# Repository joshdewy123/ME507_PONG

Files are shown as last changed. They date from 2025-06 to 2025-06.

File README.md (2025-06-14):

# ME 507 - Ping Pong Ball Launcher

**Team Members:** Josh DeWeese, Nolan Jeung  
**Support:** Charlie Refvem, Vincent Ngo, Jason Wong

---

**Link to repository:** https://github.com/joshdewy123/ME507_PONG

**Link to video:** https://youtube.com/shorts/3GikZNkVesM?feature=share

---

## Overview

This autonomous ping pong launcher is capable of both manual and automatic targeting and launching. It rotates about two axes to aim, detects objects using a TF-Luna LIDAR, and fires ping pong balls using dual flywheels. The system is built around a custom PCB featuring an STM32 microcontroller, motor drivers, and dedicated I2C lines.

The goal of this project was to create a functional and robust autonomous targeting system while designing and assembling most of the electronics and mechanical components from scratch.

---

## Hardware (Mechanical)

The robot was designed to use primarily hardware already in our possession in order to be cost-efficient, since the robot was not anticipated to pull extremely heavy loads anyways. The list of actuators and their purposes are below:

- **2x Pololu 50:1 Gearmotor (4753):** – 12V DC motor with built-in encoders to control the turret/aiming of the robot. Their reasonable size and torque made them a viable choice for this project.
- **2x Maxon DCX 22 mm OD Motors:** - 18V DC motor with no external gearbox or sensors. They are able to reach up to about 5000 RPM at nominal speeds, making them a great choice for our flywheels. Despite their nominal voltage of 18V, they were run using 12V instead to limit the necessary power redistribution of our electronics.
- **1x MG90 Servo Motor:** - simple 5V servo motor used to control ball loading and launching. Moves to certain angles dependent on the signal sent to it. They were used to push balls forward into the launcher while blocking the next ball from launching at the same time, providing the robot functionality to control when and the quantity of balls launched.

The rest of the robot was constructed using a combination of 3-D printed and off-the-shelf components. The robot implements a modular design to allow for easy re-design, removal, and reattachment of components when necessary. Power transfer between the launcher and motors was achieved using belts, pulleys, hand-cut shafts, and bearings. All fasteners are a combination of M2, M2.5, or M3 screws when necessary, and heat-set inserts were used in many locations for ease of assembly and a high overall quality of work.

Small attachment parts were made during the project’s development, and they proved to be very important. First, the flywheels were simply 3-D printed to attach to the Maxon DCX motor’s shaft, as well as be supported by bearings below. Launcher compression was achieved using super-glued foam strips around the wheels. Secondly, the different tensioners were created to improve the grip of the belt-pulley systems. On initial testing, the motors did not have enough tension with the components they were meant to move. Tensioners were added and vastly improved the power transfer of the robot.

Overall, the mechanical design of the robot worked very well. The magazine, launcher, and ball loading mechanism worked especially well. Power transfer between the motors and other components worked well, but over time, the plastic 3-D printed components began losing their grip on the metal shafts, causing more slip over time. If the project were continued with moree time and budget, the robot would utilize more metal mechanical components for longevity.

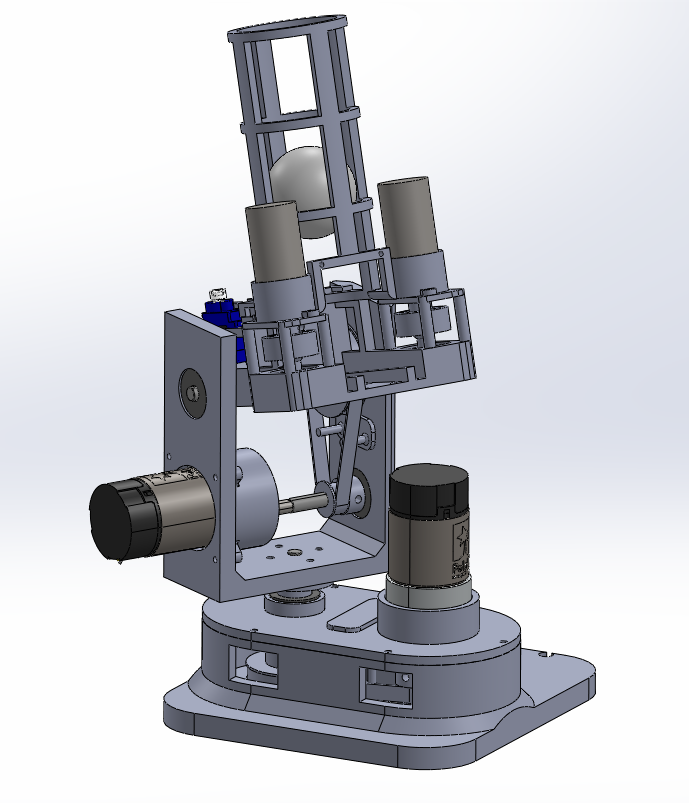
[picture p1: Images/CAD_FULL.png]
Full Mechanical System Model


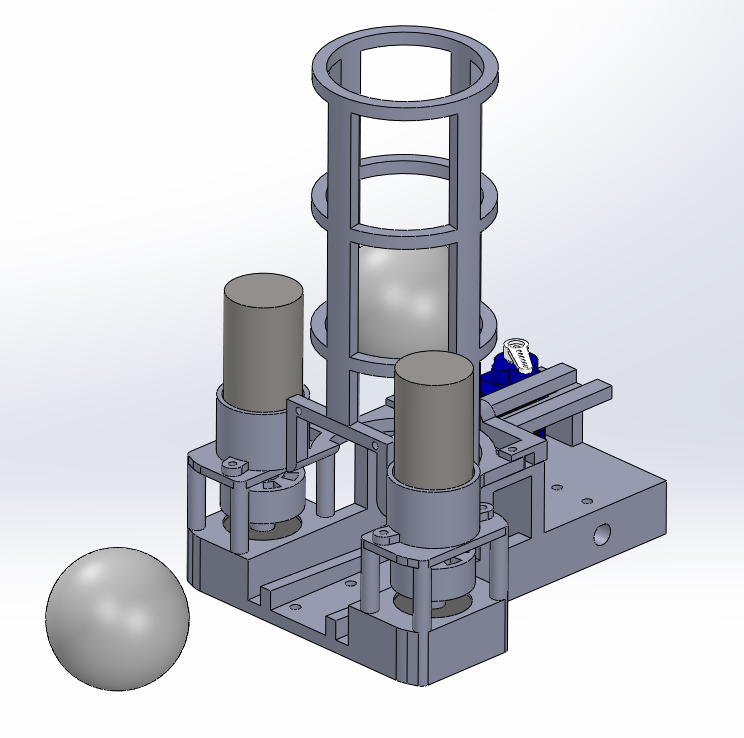
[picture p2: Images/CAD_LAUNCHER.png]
Launcher Portion of the Mechanical System Model


---

## Hardware (Electrical)

### Fusion 360 Schematics

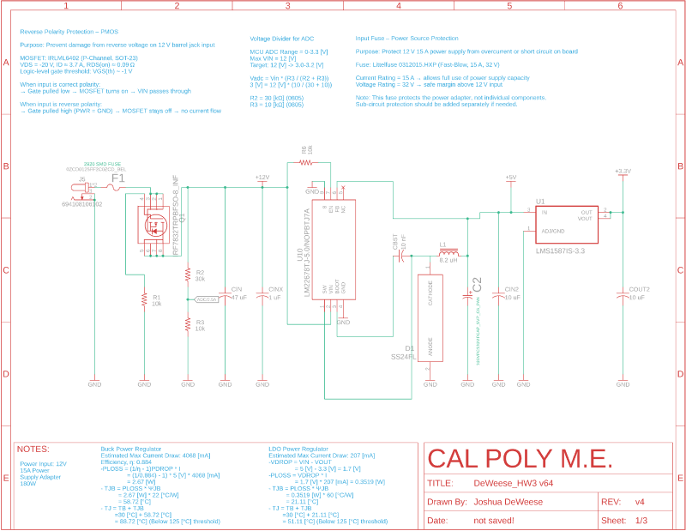
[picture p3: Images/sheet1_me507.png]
Power Regulation


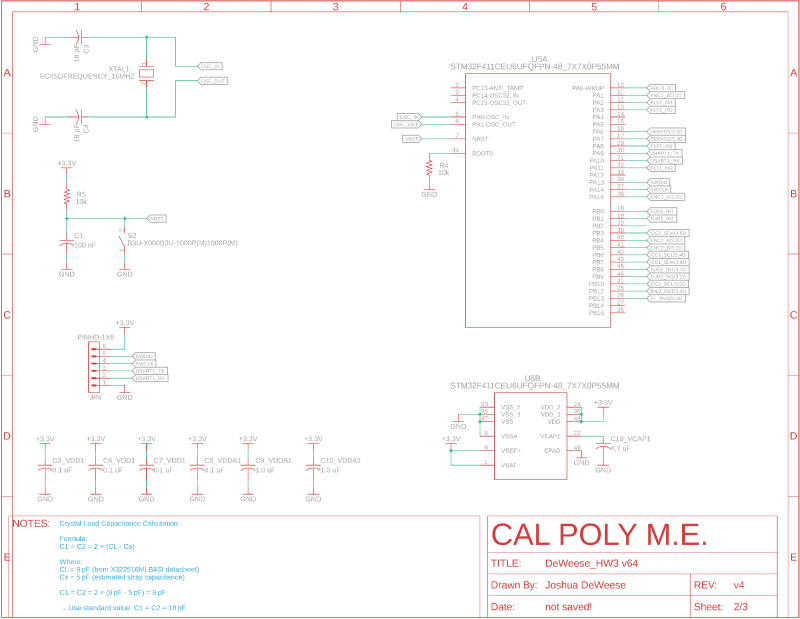
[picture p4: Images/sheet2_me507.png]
MCU Pinouts


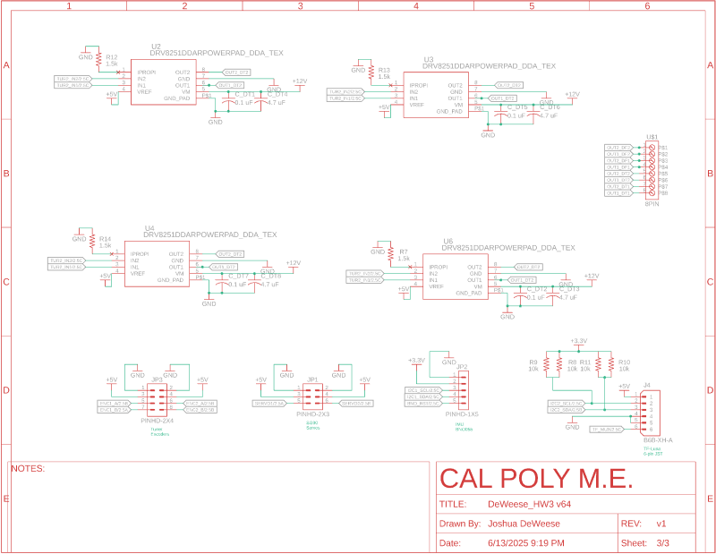
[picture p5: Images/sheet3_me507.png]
Motor Drivers w/ Sensor + Actuator Outputs


### Fusion 360 CAD Render

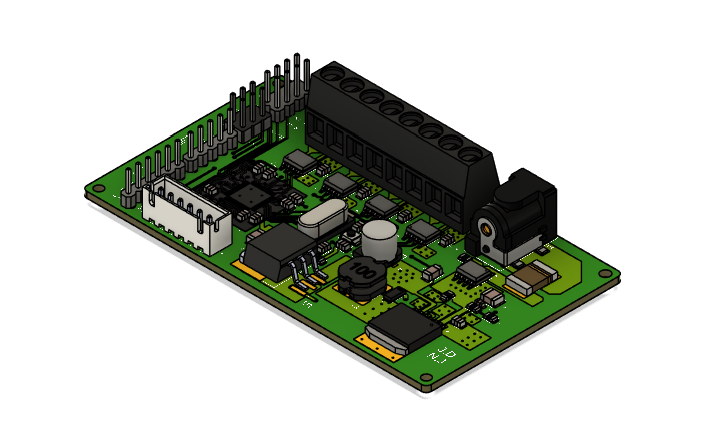
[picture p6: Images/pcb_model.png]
PCB CAD Model


### Assembled PCB - Before Hotfixes

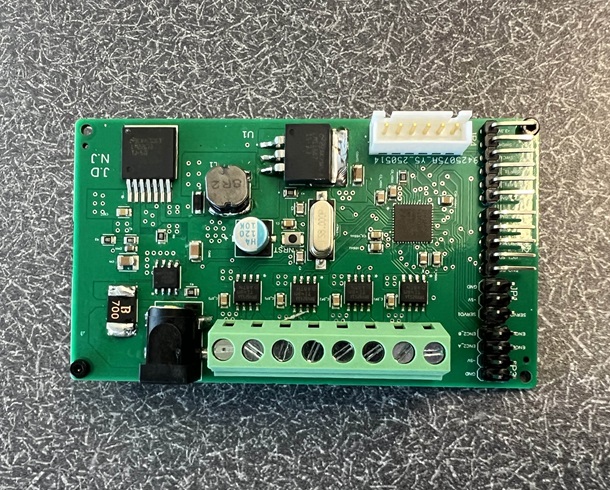
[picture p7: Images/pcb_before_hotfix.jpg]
Before Fix


### Assembled PCB - After Hotfixes

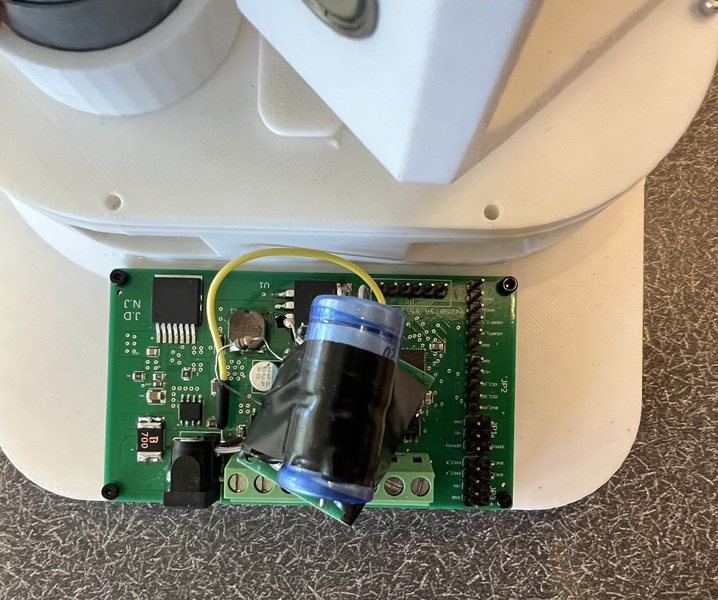
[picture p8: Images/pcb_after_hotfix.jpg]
After Fix


**This board includes:**

- STM32F411CEU6 microcontroller
- DRV8251 motor drivers
- Barrel jack for 12V input
- 5V and 3.3V rails (via Buck and LDO regulators)
- I2C, UART, and GPIO breakout headers

---

## Roadblocks and Debugging Challenges

### 1. **Motor Driver Output Failures**

**Issue:** Turret motor driver (DRV8251) failed to drive motors consistently.

**Cause:** Missing or insufficient bulk capacitance and improper IPROPI pin handling.  
**Fix:**

- Added 0.1 µF and 4.7 µF capacitors to stabilize power rails
- Pulled IPROPI to GND through a 1.5kΩ resistor

#### Fusion Schematic Before Fix

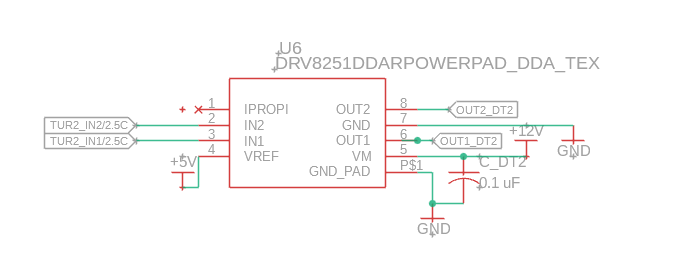
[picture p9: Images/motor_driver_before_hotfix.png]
Motor Driver Schematic Before


#### Fusion Schematic After Fix

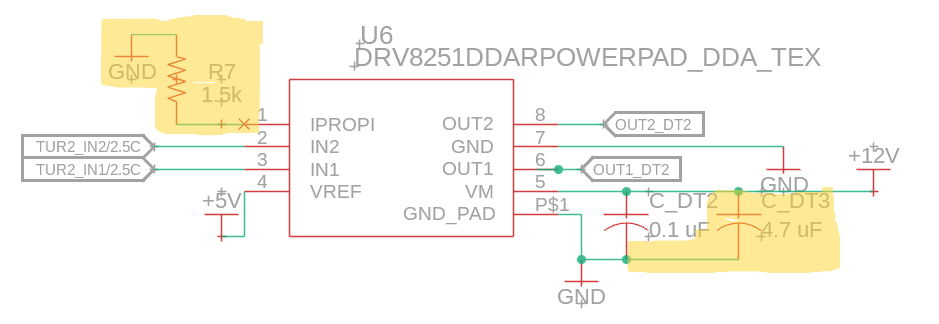
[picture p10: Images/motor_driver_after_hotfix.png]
Motor Driver Schematic After


---

### 2. **LIDAR Inconsistent I2C Behavior**

**Issue:** TF-Luna LIDAR would intermittently drop off the I2C bus.  
**Cause:** No pull-up resistors on SDA and SCL lines.  
**Fix:** Manually added 10kΩ pull-ups from both lines to 3.3V.

#### Fusion Schematic Before Fix

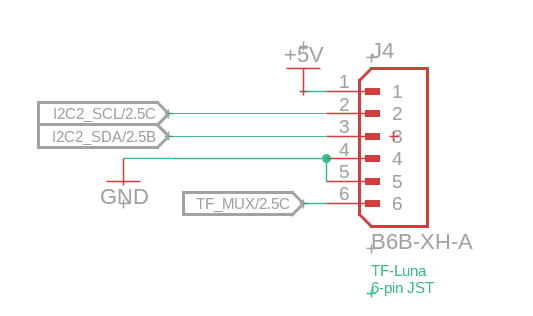
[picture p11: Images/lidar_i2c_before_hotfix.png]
LIDAR Schematic Before


#### Fusion Schematic After Fix

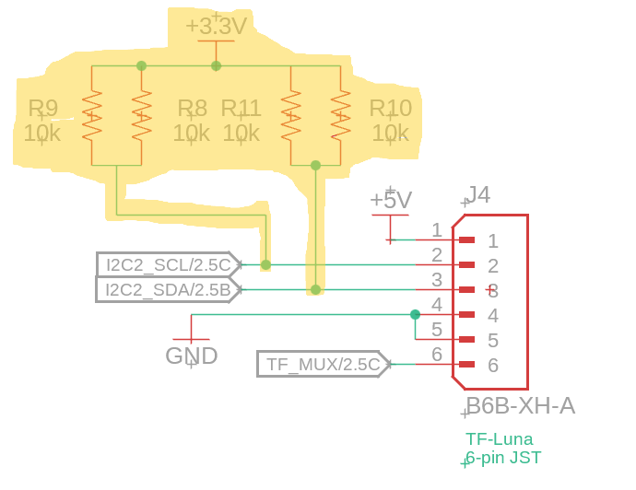
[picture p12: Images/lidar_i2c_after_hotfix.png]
LIDAR Schematic After


#### Physical Pull-up Resistor Fix (3 Angles)

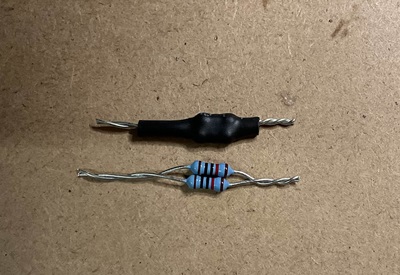
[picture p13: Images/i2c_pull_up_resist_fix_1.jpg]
Pull-up Fix 1
  
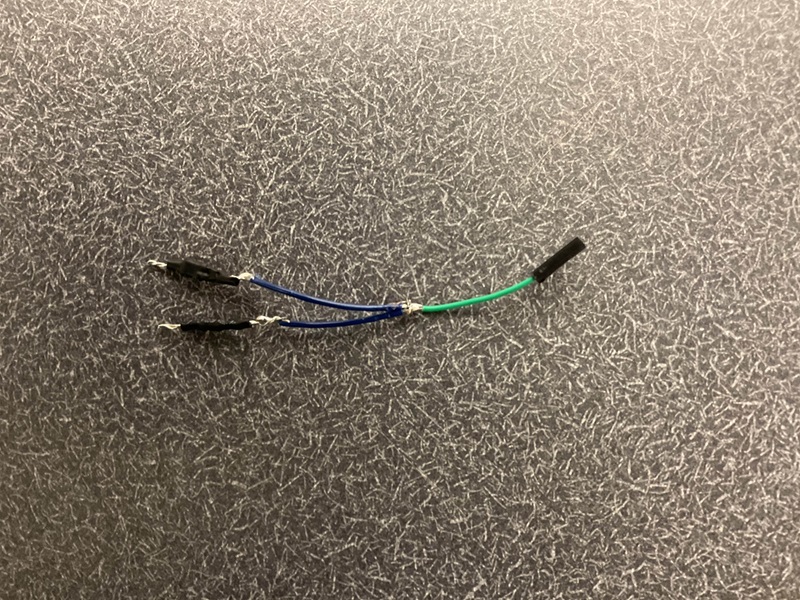
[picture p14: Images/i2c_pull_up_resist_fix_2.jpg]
Pull-up Fix 2
  
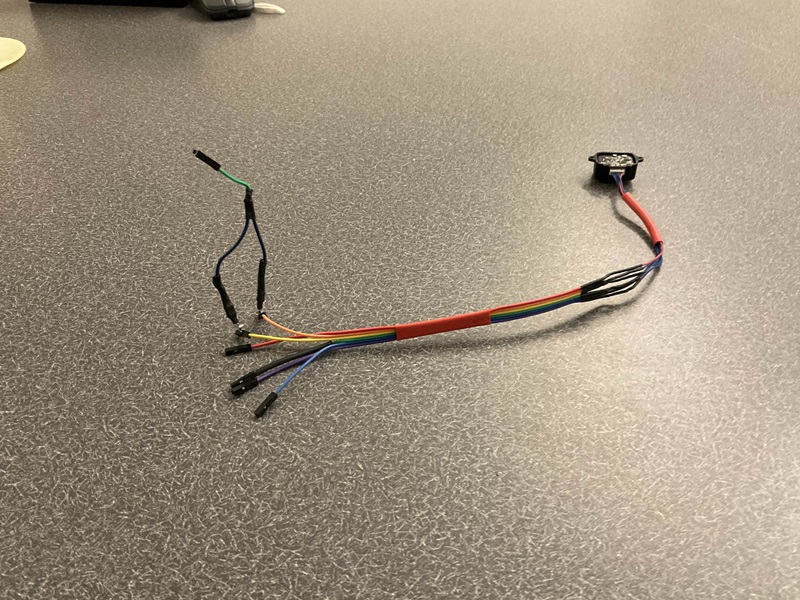
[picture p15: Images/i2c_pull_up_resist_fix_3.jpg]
Pull-up Fix 3


---

## Software Implementation

The robot was programmed in C only, as updating the project to C++ caused various issues to occur. The program features a few drivers, a primary main loop, and a finite state machine inside of the main loop. Some primary features of the program include:

- **Software PWM:** - created due to lack of timers on hardware pins for the servo motor. It functions by setting the pin to high or low depending on the system’s core clock using switch states. While this is not as accurate as hardware PWM, it was OK to use for the servo motor, since its usage was not a primary development focus and it just needed to move back and forth. However, it did cause the program to not support any HAL delays in the main loop or functions due to it causing the servo to move. This function would be removed in future iterations of the robot if possible.
- **Main Loop:** - used to run both the finite-state-machine and a few functions that always need to be called for accuracy. The main loop always updates both turret encoders and converts the ticks into degrees. It also updates the servo software pwm. If the BNO055 is implemented, it would also update the euler angles in this portion as well.
- **Finite State Machine:** - The FSM has 6 states, also described in the diagram. Entering the commands (COMM) into the console triggers different states.
- Initialization, moves the turret motors to a more optimal angle for later movements. See the link: https://youtube.com/shorts/3GikZNkVesM?feature=share
- State 1: Hub, waiting for commands to be entered in the PUTTY console
- State 2: Aim, moves the turret motors to desired angle
- State 3: Lidar, reads the current distance and amp values from the laser sensor
- State 4: Fly, spins the flywheel motors to a set duty
- State 5: Launch, launches the ball currently loaded in a sequence of movements
- State 6: Auto scan, an autonomous routine to scan the area using a set of movements and lidar scan stored data. Scans area, moves to closest distance, launches the ball, then returns to State 1.

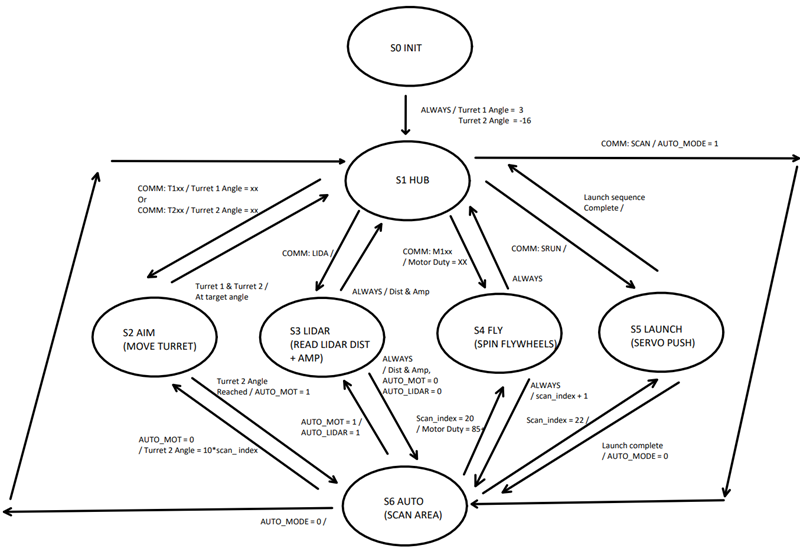
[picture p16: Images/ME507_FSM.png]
FSM Diagram


- **Commands:**
- M1xx (or M2xx) (S4): sets the duty cycle of the flywheels to the percent hex xx value.
- T1xx / T2 xx (S2): sets the desired value for the respective turret to the hex xx value.
- LIDA (S3): returns the lidar sensor values: distance (in cm) and amp (determines validity of reading).
- SRUN (S5): servo routine to launch the ball.
- SCAN (S6): autonomous scan routine

---

## Future Work

If this project were continued, there are multiple fixes to be implemented that would greatly improve the consistency and functionality of the robot:

- **Improve material choices and design:** - Physical slop between the shafts and 3-D printed components developed over time when operating the robot. By adding more metal components or inserts to connect the shafts to 3-D printed components, the removed slop would improve the encoder angle reading accuracy and ensure proper movement when intended.
- **Review datasheets to optimize PCB design:** - Because of the hotfixes implemented to make the motor drivers functional on the PCB, there were more temperature and motor driver overcurrent than intended. This sometimes caused the motors to not run when intended when the robot was left on for extended periods of time. This would also sometimes cause the robot to get stuck in certain states due to not reaching its intended motor angles. If the current sensing resistors and bulk capacitors were more properly implemented into the PCB design, the motor driver would be much more consistent, leading to easier testing and functionality over time.
- **Implement BNO055 (IMU) logic:** - Since the IMU is attached to the end of the launching mechanism, its angle readings would be more accurate than the encoder readings. It would also account for the physical slop, which the motors could then compensate for in a control loop. However, even though the IMU was functional, there was not time to implement refined control loops using the IMU readings.
- **Improve UI:** - The PUTTY console UI was usable and had all the necessary functionality. However, an actual UI using buttons instead of commands would be more intuitive. Additionally, wireless control would be beneficial for ease of use.

---

## Repository Structure

```
ME507_PONG
├── CAD_MECHANICAL_SYSTEM/      # CAD files for mechanical design
├── Core/                       # Main firmware source code (.c/.h)
├── Drivers/                    # Device drivers (e.g. HAL, custom)
├── Images/                     # Images for Doxygen/README
├── docs/                       # GitHub Pages deployment folder
│   └── index.html              # Doxygen homepage
├── .gitignore                  # Excludes build & local files
├── .project, .cproject         # Eclipse project configs
├── .mxproject                  # STM32CubeMX project file
├── README.md                   # Project overview and documentation
├── STM32F411CEUX_FLASH.ld      # Linker script (FLASH region)
├── STM32F411CEUX_RAM.ld        # Linker script (RAM region)
└── Term_Project_3.ioc          # STM32CubeMX configuration file
```

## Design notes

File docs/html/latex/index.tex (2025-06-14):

\chapter{ME 507 -\/ Ping Pong Ball Launcher }
\hypertarget{index}{}\label{index}\index{ME 507 -\/ Ping Pong Ball Launcher@{ME 507 -\/ Ping Pong Ball Launcher}}
\label{index_md__r_e_a_d_m_e}%
\Hypertarget{index_md__r_e_a_d_m_e}%

{\bfseries{Team Members\+:}} Josh De\+Weese, Nolan Jeung ~\newline
 {\bfseries{Support\+:}} Charlie Refvem, Vincent Ngo, Jason Wong

\DoxyHorRuler{0}

{\bfseries{Link to repository\+:}} \href{https://github.com/joshdewy123/ME507_PONG}{\texttt{https\+://github.\+com/joshdewy123/\+ME507\+\_\+\+PONG}}

{\bfseries{Link to video\+:}} \href{https://youtube.com/shorts/3GikZNkVesM?feature=share}{\texttt{https\+://youtube.\+com/shorts/3\+Gik\+ZNk\+Ves\+M?feature=share}}

\DoxyHorRuler{0}
\hypertarget{index_autotoc_md3}{}\doxysection{\texorpdfstring{Overview}{Overview}}\label{index_autotoc_md3}
This autonomous ping pong launcher is capable of both manual and automatic targeting and launching. It rotates about two axes to aim, detects objects using a TF-\/\+Luna LIDAR, and fires ping pong balls using dual flywheels. The system is built around a custom PCB featuring an STM32 microcontroller, motor drivers, and dedicated I2C lines.

The goal of this project was to create a functional and robust autonomous targeting system while designing and assembling most of the electronics and mechanical components from scratch.

\DoxyHorRuler{0}
\hypertarget{index_autotoc_md5}{}\doxysection{\texorpdfstring{Hardware (Mechanical)}{Hardware (Mechanical)}}\label{index_autotoc_md5}
The robot was designed to use primarily hardware already in our possession in order to be cost-\/efficient, since the robot was not anticipated to pull extremely heavy loads anyways. The list of actuators and their purposes are below\+:

\begin{DoxyItemize}
\item {\bfseries{2x Pololu 50\+:1 Gearmotor (4753)\+:}} – 12V DC motor with built-\/in encoders to control the turret/aiming of the robot. Their reasonable size and torque made them a viable choice for this project.
\item {\bfseries{2x Maxon DCX 22 mm OD Motors\+:}} -\/ 18V DC motor with no external gearbox or sensors. They are able to reach up to about 5000 RPM at nominal speeds, making them a great choice for our flywheels. Despite their nominal voltage of 18V, they were run using 12V instead to limit the necessary power redistribution of our electronics.
\item {\bfseries{1x MG90 Servo Motor\+:}} -\/ simple 5V servo motor used to control ball loading and launching. Moves to certain angles dependent on the signal sent to it. They were used to push balls forward into the launcher while blocking the next ball from launching at the same time, providing the robot functionality to control when and the quantity of balls launched.
\end{DoxyItemize}

The rest of the robot was constructed using a combination of 3-\/D printed and off-\/the-\/shelf components. The robot implements a modular design to allow for easy re-\/design, removal, and reattachment of components when necessary. Power transfer between the launcher and motors was achieved using belts, pulleys, hand-\/cut shafts, and bearings. All fasteners are a combination of M2, M2.\+5, or M3 screws when necessary, and heat-\/set inserts were used in many locations for ease of assembly and a high overall quality of work.

Small attachment parts were made during the project’s development, and they proved to be very important. First, the flywheels were simply 3-\/D printed to attach to the Maxon DCX motor’s shaft, as well as be supported by bearings below. Launcher compression was achieved using super-\/glued foam strips around the wheels. Secondly, the different tensioners were created to improve the grip of the belt-\/pulley systems. On initial testing, the motors did not have enough tension with the components they were meant to move. Tensioners were added and vastly improved the power transfer of the robot.

Overall, the mechanical design of the robot worked very well. The magazine, launcher, and ball loading mechanism worked especially well. Power transfer between the motors and other components worked well, but over time, the plastic 3-\/D printed components began losing their grip on the metal shafts, causing more slip over time. If the project were continued with moree time and budget, the robot would utilize more metal mechanical components for longevity.

\begin{DoxyImage}

\doxyfigcaption{Full Mechanical System Model}
\end{DoxyImage}

\begin{DoxyImage}

\doxyfigcaption{Launcher Portion of the Mechanical System Model}
\end{DoxyImage}

\DoxyHorRuler{0}
\hypertarget{index_autotoc_md7}{}\doxysection{\texorpdfstring{Hardware (Electrical)}{Hardware (Electrical)}}\label{index_autotoc_md7}
\hypertarget{index_autotoc_md8}{}\doxysubsection{\texorpdfstring{Fusion 360 Schematics}{Fusion 360 Schematics}}\label{index_autotoc_md8}
 
\begin{DoxyImage}

\doxyfigcaption{Power Regulation}
\end{DoxyImage}

\begin{DoxyImage}

\doxyfigcaption{MCU Pinouts}
\end{DoxyImage}

\begin{DoxyImage}

\doxyfigcaption{Motor Drivers w/ Sensor + Actuator Outputs}
\end{DoxyImage}
   \hypertarget{index_autotoc_md9}{}\doxysubsection{\texorpdfstring{Fusion 360 CAD Render}{Fusion 360 CAD Render}}\label{index_autotoc_md9}
 
\begin{DoxyImage}

\doxyfigcaption{PCB CAD Model}
\end{DoxyImage}
   \hypertarget{index_autotoc_md10}{}\doxysubsection{\texorpdfstring{Assembled PCB -\/ Before Hotfixes}{Assembled PCB -\/ Before Hotfixes}}\label{index_autotoc_md10}
 
\begin{DoxyImage}

\doxyfigcaption{Before Fix}
\end{DoxyImage}
   \hypertarget{index_autotoc_md11}{}\doxysubsection{\texorpdfstring{Assembled PCB -\/ After Hotfixes}{Assembled PCB -\/ After Hotfixes}}\label{index_autotoc_md11}
 
\begin{DoxyImage}

\doxyfigcaption{After Fix}
\end{DoxyImage}

{\bfseries{This board includes\+:}}

\begin{DoxyItemize}
\item STM32\+F411\+CEU6 microcontroller
\item DRV8251 motor drivers
\item Barrel jack for 12V input
\item 5V and 3.\+3V rails (via Buck and LDO regulators)
\item I2C, UART, and GPIO breakout headers
\end{DoxyItemize}

\DoxyHorRuler{0}
\hypertarget{index_autotoc_md13}{}\doxysection{\texorpdfstring{Roadblocks and Debugging Challenges}{Roadblocks and Debugging Challenges}}\label{index_autotoc_md13}
\hypertarget{index_autotoc_md14}{}\doxysubsection{\texorpdfstring{1. {\bfseries{Motor Driver Output Failures}}}{1. {\bfseries{Motor Driver Output Failures}}}}\label{index_autotoc_md14}
{\bfseries{Issue\+:}} Turret motor driver (DRV8251) failed to drive motors consistently.

{\bfseries{Cause\+:}} Missing or insufficient bulk capacitance and improper IPROPI pin handling. ~\newline
 {\bfseries{Fix\+:}}

\begin{DoxyItemize}
\item Added 0.\+1 µF and 4.\+7 µF capacitors to stabilize power rails
\item Pulled IPROPI to GND through a 1.\+5kΩ resistor
\end{DoxyItemize}\hypertarget{index_autotoc_md15}{}\doxysubsubsection{\texorpdfstring{Fusion Schematic Before Fix}{Fusion Schematic Before Fix}}\label{index_autotoc_md15}
 
\begin{DoxyImage}

\doxyfigcaption{Motor Driver Schematic Before}
\end{DoxyImage}
   \hypertarget{index_autotoc_md16}{}\doxysubsubsection{\texorpdfstring{Fusion Schematic After Fix}{Fusion Schematic After Fix}}\label{index_autotoc_md16}
 
\begin{DoxyImage}

\doxyfigcaption{Motor Driver Schematic After}
\end{DoxyImage}

\DoxyHorRuler{0}
\hypertarget{index_autotoc_md18}{}\doxysubsection{\texorpdfstring{2. {\bfseries{LIDAR Inconsistent I2C Behavior}}}{2. {\bfseries{LIDAR Inconsistent I2C Behavior}}}}\label{index_autotoc_md18}
{\bfseries{Issue\+:}} TF-\/\+Luna LIDAR would intermittently drop off the I2C bus. ~\newline
 {\bfseries{Cause\+:}} No pull-\/up resistors on SDA and SCL lines. ~\newline
 {\bfseries{Fix\+:}} Manually added 10kΩ pull-\/ups from both lines to 3.\+3V.\hypertarget{index_autotoc_md19}{}\doxysubsubsection{\texorpdfstring{Fusion Schematic Before Fix}{Fusion Schematic Before Fix}}\label{index_autotoc_md19}
 
\begin{DoxyImage}

\doxyfigcaption{LIDAR Schematic Before}
\end{DoxyImage}
   \hypertarget{index_autotoc_md20}{}\doxysubsubsection{\texorpdfstring{Fusion Schematic After Fix}{Fusion Schematic After Fix}}\label{index_autotoc_md20}
 
\begin{DoxyImage}

\doxyfigcaption{LIDAR Schematic After}
\end{DoxyImage}
   \hypertarget{index_autotoc_md21}{}\doxysubsubsection{\texorpdfstring{Physical Pull-\/up Resistor Fix (3 Angles)}{Physical Pull-\/up Resistor Fix (3 Angles)}}\label{index_autotoc_md21}
 
\begin{DoxyInlineImage}
%Pull-\/up Fix 1
\end{DoxyInlineImage}

~\newline
  
\begin{DoxyInlineImage}
%Pull-\/up Fix 2
\end{DoxyInlineImage}

~\newline
  
\begin{DoxyInlineImage}
%Pull-\/up Fix 3
\end{DoxyInlineImage}

\DoxyHorRuler{0}
\hypertarget{index_autotoc_md23}{}\doxysection{\texorpdfstring{Software Implementation}{Software Implementation}}\label{index_autotoc_md23}
The robot was programmed in C only, as updating the project to C++ caused various issues to occur. The program features a few drivers, a primary main loop, and a finite state machine inside of the main loop. Some primary features of the program include\+:

\begin{DoxyItemize}
\item {\bfseries{Software PWM\+:}} -\/ created due to lack of timers on hardware pins for the servo motor. It functions by setting the pin to high or low depending on the system’s core clock using switch states. While this is not as accurate as hardware PWM, it was OK to use for the servo motor, since its usage was not a primary development focus and it just needed to move back and forth. However, it did cause the program to not support any HAL delays in the main loop or functions due to it causing the servo to move. This function would be removed in future iterations of the robot if possible.
\item {\bfseries{Main Loop\+:}} -\/ used to run both the finite-\/state-\/machine and a few functions that always need to be called for accuracy. The main loop always updates both turret encoders and converts the ticks into degrees. It also updates the servo software pwm. If the BNO055 is implemented, it would also update the euler angles in this portion as well.
\item {\bfseries{Finite State Machine\+:}} -\/ The FSM has 6 states, also described in the diagram. Entering the commands (COMM) into the console triggers different states.
\item Initialization, moves the turret motors to a more optimal angle for later movements. See the link\+: \href{https://youtube.com/shorts/3GikZNkVesM?feature=share}{\texttt{https\+://youtube.\+com/shorts/3\+Gik\+ZNk\+Ves\+M?feature=share}}
\item State 1\+: Hub, waiting for commands to be entered in the PUTTY console
\item State 2\+: Aim, moves the turret motors to desired angle
\item State 3\+: Lidar, reads the current distance and amp values from the laser sensor
\item State 4\+: Fly, spins the flywheel motors to a set duty
\item State 5\+: Launch, launches the ball currently loaded in a sequence of movements
\item State 6\+: Auto scan, an autonomous routine to scan the area using a set of movements and lidar scan stored data. Scans area, moves to closest distance, launches the ball, then returns to State 1.
\end{DoxyItemize}

\begin{DoxyImage}

\doxyfigcaption{FSM Diagram}
\end{DoxyImage}

\begin{DoxyItemize}
\item {\bfseries{Commands\+:}}
\item M1xx (or M2xx) (S4)\+: sets the duty cycle of the flywheels to the percent hex xx value.
\item T1xx / T2 xx (S2)\+: sets the desired value for the respective turret to the hex xx value.
\item LIDA (S3)\+: returns the lidar sensor values\+: distance (in cm) and amp (determines validity of reading).
\item SRUN (S5)\+: servo routine to launch the ball.
\item SCAN (S6)\+: autonomous scan routine
\end{DoxyItemize}

\DoxyHorRuler{0}
\hypertarget{index_autotoc_md25}{}\doxysection{\texorpdfstring{Future Work}{Future Work}}\label{index_autotoc_md25}
If this project were continued, there are multiple fixes to be implemented that would greatly improve the consistency and functionality of the robot\+:

\begin{DoxyItemize}
\item {\bfseries{Improve material choices and design\+:}} -\/ Physical slop between the shafts and 3-\/D printed components developed over time when operating the robot. By adding more metal components or inserts to connect the shafts to 3-\/D printed components, the removed slop would improve the encoder angle reading accuracy and ensure proper movement when intended.
\item {\bfseries{Review datasheets to optimize PCB design\+:}} -\/ Because of the hotfixes implemented to make the motor drivers functional on the PCB, there were more temperature and motor driver overcurrent than intended. This sometimes caused the motors to not run when intended when the robot was left on for extended periods of time. This would also sometimes cause the robot to get stuck in certain states due to not reaching its intended motor angles. If the current sensing resistors and bulk capacitors were more properly implemented into the PCB design, the motor driver would be much more consistent, leading to easier testing and functionality over time.
\item {\bfseries{Implement BNO055 (IMU) logic\+:}} -\/ Since the IMU is attached to the end of the launching mechanism, its angle readings would be more accurate than the encoder readings. It would also account for the physical slop, which the motors could then compensate for in a control loop. However, even though the IMU was functional, there was not time to implement refined control loops using the IMU readings.
\item {\bfseries{Improve UI\+:}} -\/ The PUTTY console UI was usable and had all the necessary functionality. However, an actual UI using buttons instead of commands would be more intuitive. Additionally, wireless control would be beneficial for ease of use.
\end{DoxyItemize}

\DoxyHorRuler{0}
\hypertarget{index_autotoc_md27}{}\doxysection{\texorpdfstring{Repository Structure}{Repository Structure}}\label{index_autotoc_md27}

\begin{DoxyCode}{0}
\DoxyCodeLine{ME507\_PONG}
\DoxyCodeLine{├──\ CAD\_MECHANICAL\_SYSTEM/\ \ \ \ \ \ \#\ CAD\ files\ for\ mechanical\ design}
\DoxyCodeLine{├──\ Core/\ \ \ \ \ \ \ \ \ \ \ \ \ \ \ \ \ \ \ \ \ \ \ \#\ Main\ firmware\ source\ code\ (.c/.h)}
\DoxyCodeLine{├──\ Drivers/\ \ \ \ \ \ \ \ \ \ \ \ \ \ \ \ \ \ \ \ \#\ Device\ drivers\ (e.g.\ HAL,\ custom)}
\DoxyCodeLine{├──\ Images/\ \ \ \ \ \ \ \ \ \ \ \ \ \ \ \ \ \ \ \ \ \#\ Images\ for\ Doxygen/README}
\DoxyCodeLine{├──\ docs/\ \ \ \ \ \ \ \ \ \ \ \ \ \ \ \ \ \ \ \ \ \ \ \#\ GitHub\ Pages\ deployment\ folder}
\DoxyCodeLine{│\ \ \ └──\ index.html\ \ \ \ \ \ \ \ \ \ \ \ \ \ \#\ Doxygen\ homepage}
\DoxyCodeLine{├──\ .gitignore\ \ \ \ \ \ \ \ \ \ \ \ \ \ \ \ \ \ \#\ Excludes\ build\ \&\ local\ files}
\DoxyCodeLine{├──\ .project,\ .cproject\ \ \ \ \ \ \ \ \ \#\ Eclipse\ project\ configs}
\DoxyCodeLine{├──\ .mxproject\ \ \ \ \ \ \ \ \ \ \ \ \ \ \ \ \ \ \#\ STM32CubeMX\ project\ file}
\DoxyCodeLine{├──\ README.md\ \ \ \ \ \ \ \ \ \ \ \ \ \ \ \ \ \ \ \#\ Project\ overview\ and\ documentation}
\DoxyCodeLine{├──\ STM32F411CEUX\_FLASH.ld\ \ \ \ \ \ \#\ Linker\ script\ (FLASH\ region)}
\DoxyCodeLine{├──\ STM32F411CEUX\_RAM.ld\ \ \ \ \ \ \ \ \#\ Linker\ script\ (RAM\ region)}
\DoxyCodeLine{└──\ Term\_Project\_3.ioc\ \ \ \ \ \ \ \ \ \ \#\ STM32CubeMX\ configuration\ file}

\end{DoxyCode}

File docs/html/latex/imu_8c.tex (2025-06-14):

\doxysection{Core/\+Src/imu.c File Reference}
\hypertarget{imu_8c}{}\label{imu_8c}\index{Core/Src/imu.c@{Core/Src/imu.c}}

Source file for BNO055 IMU functions (I2C interface)  

{\ttfamily \#include "{}imu.\+h"{}}\newline
{\ttfamily \#include "{}main.\+h"{}}\newline
{\ttfamily \#include "{}stdio.\+h"{}}\newline
{\ttfamily \#include "{}string.\+h"{}}\newline
\doxysubsubsection*{Functions}
\begin{DoxyCompactItemize}
\item 
void \mbox{\hyperlink{imu_8c_a8a7c9b3e0194fcbea9de99da817ca365}{BNO055\+\_\+\+Init}} (I2\+C\+\_\+\+Handle\+Type\+Def \texorpdfstring{$\ast$}{*}hi2c)
\begin{DoxyCompactList}\small\item\em Initializes the BNO055 IMU in NDOF mode. \end{DoxyCompactList}\item 
void \mbox{\hyperlink{imu_8c_ad7ecd78362510ecfbff802bed85d1017}{BNO055\+\_\+\+Start\+Calibration}} (void)
\begin{DoxyCompactList}\small\item\em Sends serial instructions to the user to calibrate the IMU. \end{DoxyCompactList}\item 
void \mbox{\hyperlink{imu_8c_a3e577ee53e412b88193c60606ca3e260}{BNO055\+\_\+\+Read\+Calib\+Status}} (void)
\begin{DoxyCompactList}\small\item\em Reads and prints the current IMU calibration status over UART. \end{DoxyCompactList}\item 
void \mbox{\hyperlink{imu_8c_a86d0adcbede0135de88c1fd7c6ec840c}{BNO055\+\_\+\+Get\+Calib\+Status}} (uint8\+\_\+t \texorpdfstring{$\ast$}{*}sys, uint8\+\_\+t \texorpdfstring{$\ast$}{*}gyr, uint8\+\_\+t \texorpdfstring{$\ast$}{*}acc, uint8\+\_\+t \texorpdfstring{$\ast$}{*}mag)
\begin{DoxyCompactList}\small\item\em Reads the current calibration status into provided pointers. \end{DoxyCompactList}\item 
void \mbox{\hyperlink{imu_8c_afc4a25528329c383a5d29e1a3cbba73f}{BNO055\+\_\+\+Debug\+\_\+\+Read\+Gyro}} (void)
\begin{DoxyCompactList}\small\item\em Debug function that reads and prints raw gyroscope data over UART. \end{DoxyCompactList}\item 
float \mbox{\hyperlink{imu_8c_a7300824def8ed00f98e42b7da2cdb20f}{BNO055\+\_\+\+Read\+Heading}} (void)
\begin{DoxyCompactList}\small\item\em Reads the yaw heading angle from the IMU. \end{DoxyCompactList}\item 
void \mbox{\hyperlink{imu_8c_a577c08c3b3e87816cd67c06e43bcd5e0}{BNO055\+\_\+\+Read\+Euler}} (float \texorpdfstring{$\ast$}{*}heading, float \texorpdfstring{$\ast$}{*}roll, float \texorpdfstring{$\ast$}{*}pitch)
\begin{DoxyCompactList}\small\item\em Reads Euler angles (heading, roll, pitch) from the IMU. \end{DoxyCompactList}\item 
void \mbox{\hyperlink{imu_8c_a15bcaa5c1fe1118eff460b9ea9ed8c67}{BNO055\+\_\+\+Save\+Calibration\+Offsets}} (void)
\begin{DoxyCompactList}\small\item\em Debug function to print 22-\/byte calibration offset register. \end{DoxyCompactList}\end{DoxyCompactItemize}

\doxysubsection{Detailed Description}
Source file for BNO055 IMU functions (I2C interface) 

Implements configuration and data reading functions for BNO055 sensor. Output includes heading angle and full Euler orientation. The IMU was tested and confirmed functional but not yet integrated into control FSM. 

\label{doc-func-members}
\Hypertarget{imu_8c_doc-func-members}
\doxysubsection{Function Documentation}
\Hypertarget{imu_8c_afc4a25528329c383a5d29e1a3cbba73f}\index{imu.c@{imu.c}!BNO055\_Debug\_ReadGyro@{BNO055\_Debug\_ReadGyro}}
\index{BNO055\_Debug\_ReadGyro@{BNO055\_Debug\_ReadGyro}!imu.c@{imu.c}}
\doxysubsubsection{\texorpdfstring{BNO055\_Debug\_ReadGyro()}{BNO055\_Debug\_ReadGyro()}}
{\footnotesize\ttfamily \label{imu_8c_afc4a25528329c383a5d29e1a3cbba73f} 
void BNO055\+\_\+\+Debug\+\_\+\+Read\+Gyro (\begin{DoxyParamCaption}\item[{void}]{}{}\end{DoxyParamCaption})}

Debug function that reads and prints raw gyroscope data over UART. 

\Hypertarget{imu_8c_a86d0adcbede0135de88c1fd7c6ec840c}\index{imu.c@{imu.c}!BNO055\_GetCalibStatus@{BNO055\_GetCalibStatus}}
\index{BNO055\_GetCalibStatus@{BNO055\_GetCalibStatus}!imu.c@{imu.c}}
\doxysubsubsection{\texorpdfstring{BNO055\_GetCalibStatus()}{BNO055\_GetCalibStatus()}}
{\footnotesize\ttfamily \label{imu_8c_a86d0adcbede0135de88c1fd7c6ec840c} 
void BNO055\+\_\+\+Get\+Calib\+Status (\begin{DoxyParamCaption}\item[{uint8\+\_\+t \texorpdfstring{$\ast$}{*}}]{sys}{, }\item[{uint8\+\_\+t \texorpdfstring{$\ast$}{*}}]{gyr}{, }\item[{uint8\+\_\+t \texorpdfstring{$\ast$}{*}}]{acc}{, }\item[{uint8\+\_\+t \texorpdfstring{$\ast$}{*}}]{mag}{}\end{DoxyParamCaption})}

Reads the current calibration status into provided pointers. 

\begin{DoxyParams}{Parameters}
{\em sys} & Pointer to store system calibration level \\
\hline
{\em gyr} & Pointer to store gyroscope calibration level \\
\hline
{\em acc} & Pointer to store accelerometer calibration level \\
\hline
{\em mag} & Pointer to store magnetometer calibration level \\
\hline
\end{DoxyParams}
\Hypertarget{imu_8c_a8a7c9b3e0194fcbea9de99da817ca365}\index{imu.c@{imu.c}!BNO055\_Init@{BNO055\_Init}}
\index{BNO055\_Init@{BNO055\_Init}!imu.c@{imu.c}}
\doxysubsubsection{\texorpdfstring{BNO055\_Init()}{BNO055\_Init()}}
{\footnotesize\ttfamily \label{imu_8c_a8a7c9b3e0194fcbea9de99da817ca365} 
void BNO055\+\_\+\+Init (\begin{DoxyParamCaption}\item[{I2\+C\+\_\+\+Handle\+Type\+Def \texorpdfstring{$\ast$}{*}}]{hi2c}{}\end{DoxyParamCaption})}

Initializes the BNO055 IMU in NDOF mode. 

\begin{DoxyParams}{Parameters}
{\em hi2c} & Pointer to I2C handle \\
\hline
\end{DoxyParams}
\Hypertarget{imu_8c_a3e577ee53e412b88193c60606ca3e260}\index{imu.c@{imu.c}!BNO055\_ReadCalibStatus@{BNO055\_ReadCalibStatus}}
\index{BNO055\_ReadCalibStatus@{BNO055\_ReadCalibStatus}!imu.c@{imu.c}}
\doxysubsubsection{\texorpdfstring{BNO055\_ReadCalibStatus()}{BNO055\_ReadCalibStatus()}}
{\footnotesize\ttfamily \label{imu_8c_a3e577ee53e412b88193c60606ca3e260} 
void BNO055\+\_\+\+Read\+Calib\+Status (\begin{DoxyParamCaption}\item[{void}]{}{}\end{DoxyParamCaption})}

Reads and prints the current IMU calibration status over UART. 

SYS/\+GYR/\+ACC/\+MAG status values are printed via UART for debug purposes. \Hypertarget{imu_8c_a577c08c3b3e87816cd67c06e43bcd5e0}\index{imu.c@{imu.c}!BNO055\_ReadEuler@{BNO055\_ReadEuler}}
\index{BNO055\_ReadEuler@{BNO055\_ReadEuler}!imu.c@{imu.c}}
\doxysubsubsection{\texorpdfstring{BNO055\_ReadEuler()}{BNO055\_ReadEuler()}}
{\footnotesize\ttfamily \label{imu_8c_a577c08c3b3e87816cd67c06e43bcd5e0} 
void BNO055\+\_\+\+Read\+Euler (\begin{DoxyParamCaption}\item[{float \texorpdfstring{$\ast$}{*}}]{heading}{, }\item[{float \texorpdfstring{$\ast$}{*}}]{roll}{, }\item[{float \texorpdfstring{$\ast$}{*}}]{pitch}{}\end{DoxyParamCaption})}

Reads Euler angles (heading, roll, pitch) from the IMU. 

\begin{DoxyParams}{Parameters}
{\em heading} & Pointer to store heading angle (deg) \\
\hline
{\em roll} & Pointer to store roll angle (deg) \\
\hline
{\em pitch} & Pointer to store pitch angle (deg) \\
\hline
\end{DoxyParams}
\Hypertarget{imu_8c_a7300824def8ed00f98e42b7da2cdb20f}\index{imu.c@{imu.c}!BNO055\_ReadHeading@{BNO055\_ReadHeading}}
\index{BNO055\_ReadHeading@{BNO055\_ReadHeading}!imu.c@{imu.c}}
\doxysubsubsection{\texorpdfstring{BNO055\_ReadHeading()}{BNO055\_ReadHeading()}}
{\footnotesize\ttfamily \label{imu_8c_a7300824def8ed00f98e42b7da2cdb20f} 
float BNO055\+\_\+\+Read\+Heading (\begin{DoxyParamCaption}\item[{void}]{}{}\end{DoxyParamCaption})}

Reads the yaw heading angle from the IMU. 

\begin{DoxyReturn}{Returns}
Heading in degrees (0–360°), or -\/1 on error 
\end{DoxyReturn}
\Hypertarget{imu_8c_a15bcaa5c1fe1118eff460b9ea9ed8c67}\index{imu.c@{imu.c}!BNO055\_SaveCalibrationOffsets@{BNO055\_SaveCalibrationOffsets}}
\index{BNO055\_SaveCalibrationOffsets@{BNO055\_SaveCalibrationOffsets}!imu.c@{imu.c}}
\doxysubsubsection{\texorpdfstring{BNO055\_SaveCalibrationOffsets()}{BNO055\_SaveCalibrationOffsets()}}
{\footnotesize\ttfamily \label{imu_8c_a15bcaa5c1fe1118eff460b9ea9ed8c67} 
void BNO055\+\_\+\+Save\+Calibration\+Offsets (\begin{DoxyParamCaption}\item[{void}]{}{}\end{DoxyParamCaption})}

Debug function to print 22-\/byte calibration offset register. 

This can be used to save offsets for reinitialization later. \Hypertarget{imu_8c_ad7ecd78362510ecfbff802bed85d1017}\index{imu.c@{imu.c}!BNO055\_StartCalibration@{BNO055\_StartCalibration}}
\index{BNO055\_StartCalibration@{BNO055\_StartCalibration}!imu.c@{imu.c}}
\doxysubsubsection{\texorpdfstring{BNO055\_StartCalibration()}{BNO055\_StartCalibration()}}
{\footnotesize\ttfamily \label{imu_8c_ad7ecd78362510ecfbff802bed85d1017} 
void BNO055\+\_\+\+Start\+Calibration (\begin{DoxyParamCaption}\item[{void}]{}{}\end{DoxyParamCaption})}

Sends serial instructions to the user to calibrate the IMU. 

This function prints out instructions via UART to help the user perform system, gyroscope, accelerometer, and magnetometer calibration.

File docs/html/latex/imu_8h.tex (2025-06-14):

\doxysection{Core/\+Inc/imu.h File Reference}
\hypertarget{imu_8h}{}\label{imu_8h}\index{Core/Inc/imu.h@{Core/Inc/imu.h}}

Interface for BNO055 IMU sensor over I2C.  

{\ttfamily \#include "{}stm32f4xx\+\_\+hal.\+h"{}}\newline
\doxysubsubsection*{Macros}
\begin{DoxyCompactItemize}
\item 
\#define \mbox{\hyperlink{imu_8h_af99e6b0453d87e52e02f5456095aaac0}{BNO055\+\_\+\+ADDR}}~(0x28 $<$$<$ 1)
\end{DoxyCompactItemize}
\doxysubsubsection*{Functions}
\begin{DoxyCompactItemize}
\item 
void \mbox{\hyperlink{imu_8h_a8a7c9b3e0194fcbea9de99da817ca365}{BNO055\+\_\+\+Init}} (I2\+C\+\_\+\+Handle\+Type\+Def \texorpdfstring{$\ast$}{*}hi2c)
\begin{DoxyCompactList}\small\item\em Initializes the BNO055 IMU in NDOF mode. \end{DoxyCompactList}\item 
void \mbox{\hyperlink{imu_8h_ad7ecd78362510ecfbff802bed85d1017}{BNO055\+\_\+\+Start\+Calibration}} (void)
\begin{DoxyCompactList}\small\item\em Sends serial instructions to the user to calibrate the IMU. \end{DoxyCompactList}\item 
void \mbox{\hyperlink{imu_8h_a3e577ee53e412b88193c60606ca3e260}{BNO055\+\_\+\+Read\+Calib\+Status}} (void)
\begin{DoxyCompactList}\small\item\em Reads and prints the current IMU calibration status over UART. \end{DoxyCompactList}\item 
void \mbox{\hyperlink{imu_8h_a86d0adcbede0135de88c1fd7c6ec840c}{BNO055\+\_\+\+Get\+Calib\+Status}} (uint8\+\_\+t \texorpdfstring{$\ast$}{*}sys, uint8\+\_\+t \texorpdfstring{$\ast$}{*}gyr, uint8\+\_\+t \texorpdfstring{$\ast$}{*}acc, uint8\+\_\+t \texorpdfstring{$\ast$}{*}mag)
\begin{DoxyCompactList}\small\item\em Reads the current calibration status into provided pointers. \end{DoxyCompactList}\item 
void \mbox{\hyperlink{imu_8h_afc4a25528329c383a5d29e1a3cbba73f}{BNO055\+\_\+\+Debug\+\_\+\+Read\+Gyro}} (void)
\begin{DoxyCompactList}\small\item\em Debug function that reads and prints raw gyroscope data over UART. \end{DoxyCompactList}\item 
float \mbox{\hyperlink{imu_8h_a7300824def8ed00f98e42b7da2cdb20f}{BNO055\+\_\+\+Read\+Heading}} (void)
\begin{DoxyCompactList}\small\item\em Reads the yaw heading angle from the IMU. \end{DoxyCompactList}\item 
void \mbox{\hyperlink{imu_8h_a577c08c3b3e87816cd67c06e43bcd5e0}{BNO055\+\_\+\+Read\+Euler}} (float \texorpdfstring{$\ast$}{*}heading, float \texorpdfstring{$\ast$}{*}roll, float \texorpdfstring{$\ast$}{*}pitch)
\begin{DoxyCompactList}\small\item\em Reads Euler angles (heading, roll, pitch) from the IMU. \end{DoxyCompactList}\item 
void \mbox{\hyperlink{imu_8h_a15bcaa5c1fe1118eff460b9ea9ed8c67}{BNO055\+\_\+\+Save\+Calibration\+Offsets}} (void)
\begin{DoxyCompactList}\small\item\em Debug function to print 22-\/byte calibration offset register. \end{DoxyCompactList}\end{DoxyCompactItemize}

\doxysubsection{Detailed Description}
Interface for BNO055 IMU sensor over I2C. 

This module provides initialization, calibration, and data retrieval functions for the BNO055 inertial measurement unit (IMU), configured in NDOF mode for Euler angle output.

Although IMU functionality was verified and outputs correct heading values, it was not integrated into the main FSM due to time constraints. Future work may involve using the IMU heading to actively stabilize turret orientation or detect drift during autonomous aiming. 

\label{doc-define-members}
\Hypertarget{imu_8h_doc-define-members}
\doxysubsection{Macro Definition Documentation}
\Hypertarget{imu_8h_af99e6b0453d87e52e02f5456095aaac0}\index{imu.h@{imu.h}!BNO055\_ADDR@{BNO055\_ADDR}}
\index{BNO055\_ADDR@{BNO055\_ADDR}!imu.h@{imu.h}}
\doxysubsubsection{\texorpdfstring{BNO055\_ADDR}{BNO055\_ADDR}}
{\footnotesize\ttfamily \label{imu_8h_af99e6b0453d87e52e02f5456095aaac0} 
\#define BNO055\+\_\+\+ADDR~(0x28 $<$$<$ 1)}

\label{doc-func-members}
\Hypertarget{imu_8h_doc-func-members}
\doxysubsection{Function Documentation}
\Hypertarget{imu_8h_afc4a25528329c383a5d29e1a3cbba73f}\index{imu.h@{imu.h}!BNO055\_Debug\_ReadGyro@{BNO055\_Debug\_ReadGyro}}
\index{BNO055\_Debug\_ReadGyro@{BNO055\_Debug\_ReadGyro}!imu.h@{imu.h}}
\doxysubsubsection{\texorpdfstring{BNO055\_Debug\_ReadGyro()}{BNO055\_Debug\_ReadGyro()}}
{\footnotesize\ttfamily \label{imu_8h_afc4a25528329c383a5d29e1a3cbba73f} 
void BNO055\+\_\+\+Debug\+\_\+\+Read\+Gyro (\begin{DoxyParamCaption}\item[{void}]{}{}\end{DoxyParamCaption})}

Debug function that reads and prints raw gyroscope data over UART. 

\Hypertarget{imu_8h_a86d0adcbede0135de88c1fd7c6ec840c}\index{imu.h@{imu.h}!BNO055\_GetCalibStatus@{BNO055\_GetCalibStatus}}
\index{BNO055\_GetCalibStatus@{BNO055\_GetCalibStatus}!imu.h@{imu.h}}
\doxysubsubsection{\texorpdfstring{BNO055\_GetCalibStatus()}{BNO055\_GetCalibStatus()}}
{\footnotesize\ttfamily \label{imu_8h_a86d0adcbede0135de88c1fd7c6ec840c} 
void BNO055\+\_\+\+Get\+Calib\+Status (\begin{DoxyParamCaption}\item[{uint8\+\_\+t \texorpdfstring{$\ast$}{*}}]{sys}{, }\item[{uint8\+\_\+t \texorpdfstring{$\ast$}{*}}]{gyr}{, }\item[{uint8\+\_\+t \texorpdfstring{$\ast$}{*}}]{acc}{, }\item[{uint8\+\_\+t \texorpdfstring{$\ast$}{*}}]{mag}{}\end{DoxyParamCaption})}

Reads the current calibration status into provided pointers. 

\begin{DoxyParams}{Parameters}
{\em sys} & Pointer to store system calibration level \\
\hline
{\em gyr} & Pointer to store gyroscope calibration level \\
\hline
{\em acc} & Pointer to store accelerometer calibration level \\
\hline
{\em mag} & Pointer to store magnetometer calibration level \\
\hline
\end{DoxyParams}
\Hypertarget{imu_8h_a8a7c9b3e0194fcbea9de99da817ca365}\index{imu.h@{imu.h}!BNO055\_Init@{BNO055\_Init}}
\index{BNO055\_Init@{BNO055\_Init}!imu.h@{imu.h}}
\doxysubsubsection{\texorpdfstring{BNO055\_Init()}{BNO055\_Init()}}
{\footnotesize\ttfamily \label{imu_8h_a8a7c9b3e0194fcbea9de99da817ca365} 
void BNO055\+\_\+\+Init (\begin{DoxyParamCaption}\item[{I2\+C\+\_\+\+Handle\+Type\+Def \texorpdfstring{$\ast$}{*}}]{hi2c}{}\end{DoxyParamCaption})}

Initializes the BNO055 IMU in NDOF mode. 

\begin{DoxyParams}{Parameters}
{\em hi2c} & Pointer to I2C handle \\
\hline
\end{DoxyParams}
\Hypertarget{imu_8h_a3e577ee53e412b88193c60606ca3e260}\index{imu.h@{imu.h}!BNO055\_ReadCalibStatus@{BNO055\_ReadCalibStatus}}
\index{BNO055\_ReadCalibStatus@{BNO055\_ReadCalibStatus}!imu.h@{imu.h}}
\doxysubsubsection{\texorpdfstring{BNO055\_ReadCalibStatus()}{BNO055\_ReadCalibStatus()}}
{\footnotesize\ttfamily \label{imu_8h_a3e577ee53e412b88193c60606ca3e260} 
void BNO055\+\_\+\+Read\+Calib\+Status (\begin{DoxyParamCaption}\item[{void}]{}{}\end{DoxyParamCaption})}

Reads and prints the current IMU calibration status over UART. 

SYS/\+GYR/\+ACC/\+MAG status values are printed via UART for debug purposes. \Hypertarget{imu_8h_a577c08c3b3e87816cd67c06e43bcd5e0}\index{imu.h@{imu.h}!BNO055\_ReadEuler@{BNO055\_ReadEuler}}
\index{BNO055\_ReadEuler@{BNO055\_ReadEuler}!imu.h@{imu.h}}
\doxysubsubsection{\texorpdfstring{BNO055\_ReadEuler()}{BNO055\_ReadEuler()}}
{\footnotesize\ttfamily \label{imu_8h_a577c08c3b3e87816cd67c06e43bcd5e0} 
void BNO055\+\_\+\+Read\+Euler (\begin{DoxyParamCaption}\item[{float \texorpdfstring{$\ast$}{*}}]{heading}{, }\item[{float \texorpdfstring{$\ast$}{*}}]{roll}{, }\item[{float \texorpdfstring{$\ast$}{*}}]{pitch}{}\end{DoxyParamCaption})}

Reads Euler angles (heading, roll, pitch) from the IMU. 

\begin{DoxyParams}{Parameters}
{\em heading} & Pointer to store heading angle (deg) \\
\hline
{\em roll} & Pointer to store roll angle (deg) \\
\hline
{\em pitch} & Pointer to store pitch angle (deg) \\
\hline
\end{DoxyParams}
\Hypertarget{imu_8h_a7300824def8ed00f98e42b7da2cdb20f}\index{imu.h@{imu.h}!BNO055\_ReadHeading@{BNO055\_ReadHeading}}
\index{BNO055\_ReadHeading@{BNO055\_ReadHeading}!imu.h@{imu.h}}
\doxysubsubsection{\texorpdfstring{BNO055\_ReadHeading()}{BNO055\_ReadHeading()}}
{\footnotesize\ttfamily \label{imu_8h_a7300824def8ed00f98e42b7da2cdb20f} 
float BNO055\+\_\+\+Read\+Heading (\begin{DoxyParamCaption}\item[{void}]{}{}\end{DoxyParamCaption})}

Reads the yaw heading angle from the IMU. 

\begin{DoxyReturn}{Returns}
Heading in degrees (0–360°), or -\/1 on error 
\end{DoxyReturn}
\Hypertarget{imu_8h_a15bcaa5c1fe1118eff460b9ea9ed8c67}\index{imu.h@{imu.h}!BNO055\_SaveCalibrationOffsets@{BNO055\_SaveCalibrationOffsets}}
\index{BNO055\_SaveCalibrationOffsets@{BNO055\_SaveCalibrationOffsets}!imu.h@{imu.h}}
\doxysubsubsection{\texorpdfstring{BNO055\_SaveCalibrationOffsets()}{BNO055\_SaveCalibrationOffsets()}}
{\footnotesize\ttfamily \label{imu_8h_a15bcaa5c1fe1118eff460b9ea9ed8c67} 
void BNO055\+\_\+\+Save\+Calibration\+Offsets (\begin{DoxyParamCaption}\item[{void}]{}{}\end{DoxyParamCaption})}

Debug function to print 22-\/byte calibration offset register. 

This can be used to save offsets for reinitialization later. \Hypertarget{imu_8h_ad7ecd78362510ecfbff802bed85d1017}\index{imu.h@{imu.h}!BNO055\_StartCalibration@{BNO055\_StartCalibration}}
\index{BNO055\_StartCalibration@{BNO055\_StartCalibration}!imu.h@{imu.h}}
\doxysubsubsection{\texorpdfstring{BNO055\_StartCalibration()}{BNO055\_StartCalibration()}}
{\footnotesize\ttfamily \label{imu_8h_ad7ecd78362510ecfbff802bed85d1017} 
void BNO055\+\_\+\+Start\+Calibration (\begin{DoxyParamCaption}\item[{void}]{}{}\end{DoxyParamCaption})}

Sends serial instructions to the user to calibrate the IMU. 

This function prints out instructions via UART to help the user perform system, gyroscope, accelerometer, and magnetometer calibration.

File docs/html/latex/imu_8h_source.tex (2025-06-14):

\doxysection{imu.\+h}
\hypertarget{imu_8h_source}{}\label{imu_8h_source}\index{Core/Inc/imu.h@{Core/Inc/imu.h}}
\mbox{\hyperlink{imu_8h}{Go to the documentation of this file.}}
\begin{DoxyCode}{0}
\DoxyCodeLine{00001\ }
\DoxyCodeLine{00012\ }
\DoxyCodeLine{00013\ \textcolor{preprocessor}{\#ifndef\ INC\_IMU\_H\_}}
\DoxyCodeLine{00014\ \textcolor{preprocessor}{\#define\ INC\_IMU\_H\_}}
\DoxyCodeLine{00015\ }
\DoxyCodeLine{00016\ \textcolor{preprocessor}{\#include\ "{}stm32f4xx\_hal.h"{}}}
\DoxyCodeLine{00017\ }
\DoxyCodeLine{00018\ \textcolor{preprocessor}{\#define\ BNO055\_ADDR\ (0x28\ <<\ 1)\ \ }\textcolor{comment}{//\ 7-\/bit\ address,\ shifted\ for\ HAL}}
\DoxyCodeLine{00019\ }
\DoxyCodeLine{00024\ \textcolor{keywordtype}{void}\ \mbox{\hyperlink{imu_8h_a8a7c9b3e0194fcbea9de99da817ca365}{BNO055\_Init}}(I2C\_HandleTypeDef\ *hi2c);}
\DoxyCodeLine{00025\ }
\DoxyCodeLine{00032\ \textcolor{keywordtype}{void}\ \mbox{\hyperlink{imu_8h_ad7ecd78362510ecfbff802bed85d1017}{BNO055\_StartCalibration}}(\textcolor{keywordtype}{void});}
\DoxyCodeLine{00033\ }
\DoxyCodeLine{00039\ \textcolor{keywordtype}{void}\ \mbox{\hyperlink{imu_8h_a3e577ee53e412b88193c60606ca3e260}{BNO055\_ReadCalibStatus}}(\textcolor{keywordtype}{void});}
\DoxyCodeLine{00040\ }
\DoxyCodeLine{00048\ \textcolor{keywordtype}{void}\ \mbox{\hyperlink{imu_8h_a86d0adcbede0135de88c1fd7c6ec840c}{BNO055\_GetCalibStatus}}(uint8\_t*\ sys,\ uint8\_t*\ gyr,\ uint8\_t*\ acc,\ uint8\_t*\ mag);}
\DoxyCodeLine{00049\ }
\DoxyCodeLine{00053\ \textcolor{keywordtype}{void}\ \mbox{\hyperlink{imu_8h_afc4a25528329c383a5d29e1a3cbba73f}{BNO055\_Debug\_ReadGyro}}(\textcolor{keywordtype}{void});}
\DoxyCodeLine{00054\ }
\DoxyCodeLine{00059\ \textcolor{keywordtype}{float}\ \mbox{\hyperlink{imu_8h_a7300824def8ed00f98e42b7da2cdb20f}{BNO055\_ReadHeading}}(\textcolor{keywordtype}{void});}
\DoxyCodeLine{00060\ }
\DoxyCodeLine{00067\ \textcolor{keywordtype}{void}\ \mbox{\hyperlink{imu_8h_a577c08c3b3e87816cd67c06e43bcd5e0}{BNO055\_ReadEuler}}(\textcolor{keywordtype}{float}*\ heading,\ \textcolor{keywordtype}{float}*\ roll,\ \textcolor{keywordtype}{float}*\ pitch);}
\DoxyCodeLine{00068\ }
\DoxyCodeLine{00074\ \textcolor{keywordtype}{void}\ \mbox{\hyperlink{imu_8h_a15bcaa5c1fe1118eff460b9ea9ed8c67}{BNO055\_SaveCalibrationOffsets}}(\textcolor{keywordtype}{void});}
\DoxyCodeLine{00075\ }
\DoxyCodeLine{00076\ \textcolor{preprocessor}{\#endif\ }\textcolor{comment}{/*\ INC\_IMU\_H\_\ */}\textcolor{preprocessor}{}}

\end{DoxyCode}

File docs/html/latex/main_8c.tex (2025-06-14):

\doxysection{Core/\+Src/main.c File Reference}
\hypertarget{main_8c}{}\label{main_8c}\index{Core/Src/main.c@{Core/Src/main.c}}

Application entry point for ping pong launcher project.  

{\ttfamily \#include "{}main.\+h"{}}\newline
{\ttfamily \#include "{}motor.\+h"{}}\newline
{\ttfamily \#include "{}imu.\+h"{}}\newline
{\ttfamily \#include $<$math.\+h$>$}\newline
{\ttfamily \#include $<$stdio.\+h$>$}\newline
{\ttfamily \#include $<$stdint.\+h$>$}\newline
{\ttfamily \#include $<$stdlib.\+h$>$}\newline
{\ttfamily \#include $<$string.\+h$>$}\newline
{\ttfamily \#include $<$ctype.\+h$>$}\newline
\doxysubsubsection*{Macros}
\begin{DoxyCompactItemize}
\item 
\#define \mbox{\hyperlink{main_8c_a29671976836ee7a005ffc3b83cc9900a}{CPR\+\_\+\+TURRET}}~3200
\item 
\#define \mbox{\hyperlink{main_8c_a739a2a1a0047c98ac1b18ecd25dac092}{RX\+\_\+\+BUFFER\+\_\+\+SIZE}}~7
\end{DoxyCompactItemize}
\doxysubsubsection*{Enumerations}
\begin{DoxyCompactItemize}
\item 
enum \mbox{\hyperlink{main_8c_ae2946618e700f814e6147195c808f4c8}{State\+\_\+t}} \{ \newline
\mbox{\hyperlink{main_8c_ae2946618e700f814e6147195c808f4c8a830154cdb7fd42f54f25f9f428c2538d}{STATE\+\_\+0}}
, \mbox{\hyperlink{main_8c_ae2946618e700f814e6147195c808f4c8a3be8ff1b14d8f456ec4f53f6ce5790fa}{STATE\+\_\+1}}
, \mbox{\hyperlink{main_8c_ae2946618e700f814e6147195c808f4c8acd69fec890fc58a3ce12d157e80ab7cc}{STATE\+\_\+2}}
, \mbox{\hyperlink{main_8c_ae2946618e700f814e6147195c808f4c8ac2afcd17617ae1ecba56029ff6c22e38}{STATE\+\_\+3}}
, \newline
\mbox{\hyperlink{main_8c_ae2946618e700f814e6147195c808f4c8aa7e03e808984be120062b5e590333028}{STATE\+\_\+4}}
, \mbox{\hyperlink{main_8c_ae2946618e700f814e6147195c808f4c8a247a852e037bd71e9c372e4cae5375a8}{STATE\+\_\+5}}
, \mbox{\hyperlink{main_8c_ae2946618e700f814e6147195c808f4c8a1368a98786e7c54b0b1f078dedb08cb6}{STATE\+\_\+6}}
 \}
\end{DoxyCompactItemize}
\doxysubsubsection*{Functions}
\begin{DoxyCompactItemize}
\item 
void \mbox{\hyperlink{main_8c_a70af21c671abfcc773614a9a4f63d920}{System\+Clock\+\_\+\+Config}} (void)
\begin{DoxyCompactList}\small\item\em System Clock Configuration. \end{DoxyCompactList}\item 
void \mbox{\hyperlink{main_8c_ade14a2f86085d70042e21b719d09b2fe}{dwt\+\_\+init}} (void)
\item 
void \mbox{\hyperlink{main_8c_a161515d302eceb8f79859465cadcdbc0}{servo\+\_\+pwm\+\_\+update}} (void)
\item 
int \mbox{\hyperlink{main_8c_a840291bc02cba5474a4cb46a9b9566fe}{main}} (void)
\begin{DoxyCompactList}\small\item\em Main entry point — configures peripherals and enters control loop. \end{DoxyCompactList}\item 
void \mbox{\hyperlink{main_8c_ae494a9643f29b87d6d81e5264e60e57b}{HAL\+\_\+\+UART\+\_\+\+Rx\+Cplt\+Callback}} (UART\+\_\+\+Handle\+Type\+Def \texorpdfstring{$\ast$}{*}huart)
\item 
void \mbox{\hyperlink{main_8c_a1730ffe1e560465665eb47d9264826f9}{Error\+\_\+\+Handler}} (void)
\begin{DoxyCompactList}\small\item\em This function is executed in case of error occurrence. \end{DoxyCompactList}\end{DoxyCompactItemize}
\doxysubsubsection*{Variables}
\begin{DoxyCompactItemize}
\item 
I2\+C\+\_\+\+Handle\+Type\+Def \mbox{\hyperlink{main_8c_ac379bcc152d860f08b1279fd3e232295}{hi2c2}}
\item 
volatile uint8\+\_\+t \mbox{\hyperlink{main_8c_a79c01541f789e6b0e9da9bd118ef1681}{imu\+\_\+mode}} = 0
\item 
volatile uint8\+\_\+t \mbox{\hyperlink{main_8c_a26e06bee38154c3e3480c6f6b723f059}{calib\+\_\+mode}} = 0
\item 
volatile uint8\+\_\+t \mbox{\hyperlink{main_8c_adce9412a27849ba591609b337dbc1369}{lidar\+\_\+mode}} = 0
\item 
uint8\+\_\+t \mbox{\hyperlink{main_8c_a5c1c771a6bca2a8939852e597c8054f6}{lidar\+\_\+buf}} \mbox{[}4\mbox{]}
\item 
ADC\+\_\+\+Handle\+Type\+Def \mbox{\hyperlink{main_8c_a22b804736f5648d52f639b2647d4ed13}{hadc1}}
\item 
I2\+C\+\_\+\+Handle\+Type\+Def \mbox{\hyperlink{main_8c_af7b2c26e44dadaaa798a5c3d82914ba7}{hi2c1}}
\item 
TIM\+\_\+\+Handle\+Type\+Def \mbox{\hyperlink{main_8c_a25fc663547539bc49fecc0011bd76ab5}{htim1}}
\item 
TIM\+\_\+\+Handle\+Type\+Def \mbox{\hyperlink{main_8c_a2c80fd5510e2990a59a5c90d745c716c}{htim2}}
\item 
TIM\+\_\+\+Handle\+Type\+Def \mbox{\hyperlink{main_8c_aac3d2c59ee0e3bbae1b99529a154eb62}{htim3}}
\item 
TIM\+\_\+\+Handle\+Type\+Def \mbox{\hyperlink{main_8c_a31f6f787777409af5ed0d131b52b7988}{htim9}}
\item 
TIM\+\_\+\+Handle\+Type\+Def \mbox{\hyperlink{main_8c_a3c386e4f1937c518c1beccddef92045e}{htim10}}
\item 
TIM\+\_\+\+Handle\+Type\+Def \mbox{\hyperlink{main_8c_a2f22f985c4f33318fdcd4cc996623bf4}{htim11}}
\item 
UART\+\_\+\+Handle\+Type\+Def \mbox{\hyperlink{main_8c_a2cf715bef37f7e8ef385a30974a5f0d5}{huart1}}
\begin{DoxyCompactList}\small\item\em UART interface used for IMU debug and user command output. \end{DoxyCompactList}\item 
int32\+\_\+t \mbox{\hyperlink{main_8c_a7575fff8f1cf20db06571845911ac5ac}{duty\+\_\+flywheel1}} = 0
\item 
int32\+\_\+t \mbox{\hyperlink{main_8c_aaa2a7153eb2feab6c30fa192364f0a8a}{duty\+\_\+flywheel2}} = 0
\item 
int32\+\_\+t \mbox{\hyperlink{main_8c_adbe25b24634a71fe4a900547f7e7d99e}{duty\+\_\+turret1}} = 0
\item 
int32\+\_\+t \mbox{\hyperlink{main_8c_a698674f38793dd9795ca6b8bd25c2918}{duty\+\_\+turret2}} = 0
\item 
int32\+\_\+t \mbox{\hyperlink{main_8c_a21a2e91d2dbeb89285478c49a0345f88}{turret1\+\_\+enc\+\_\+count}} = 0
\item 
int32\+\_\+t \mbox{\hyperlink{main_8c_a499be0edd8a3637fe08a286309cd5dbe}{turret1\+\_\+enc\+\_\+deg}} = 0
\item 
int32\+\_\+t \mbox{\hyperlink{main_8c_a1003878a23fa8103d73429ffcc76c37b}{turret1\+\_\+target}} = 0
\item 
int32\+\_\+t \mbox{\hyperlink{main_8c_ae5d31aeb9915e39f86126cb0c2c377bb}{turret2\+\_\+enc\+\_\+pos}} = 0
\item 
int32\+\_\+t \mbox{\hyperlink{main_8c_a75ae1024ee7b8619b381e417164583f4}{turret2\+\_\+enc\+\_\+deg}} = 0
\item 
int32\+\_\+t \mbox{\hyperlink{main_8c_a87c4df08862c1ffe52dbabbcf7cb400e}{turret2\+\_\+target}} = 0
\item 
\mbox{\hyperlink{structmotor__t}{motor\+\_\+t}} \mbox{\hyperlink{main_8c_a6fa872f737d1eb3797b06ad86b910797}{flywheel1}}
\item 
\mbox{\hyperlink{structmotor__t}{motor\+\_\+t}} \mbox{\hyperlink{main_8c_a1f60edf44bd9bde71ef7aae8d5863db2}{flywheel2}}
\item 
\mbox{\hyperlink{structmotor__t}{motor\+\_\+t}} \mbox{\hyperlink{main_8c_a78c6167d8d0b21108c8e9a38f9ce05ff}{turret1}}
\item 
\mbox{\hyperlink{structmotor__t}{motor\+\_\+t}} \mbox{\hyperlink{main_8c_acfa9c01b03001c8c48f6885ef5fdd1e5}{turret2}}
\item 
\mbox{\hyperlink{fsm_8h_ae2946618e700f814e6147195c808f4c8}{State\+\_\+t}} \mbox{\hyperlink{main_8c_aae419efef4a0d2b1a7ad68cb49a42389}{current\+\_\+state}} = \mbox{\hyperlink{fsm_8h_ae2946618e700f814e6147195c808f4c8a830154cdb7fd42f54f25f9f428c2538d}{STATE\+\_\+0}}
\item 
uint8\+\_\+t \mbox{\hyperlink{main_8c_a4d10e67794e6818e6b092b567855831c}{auto\+\_\+mode}} = 0
\item 
uint8\+\_\+t \mbox{\hyperlink{main_8c_a080f3cf5f32d36259f3e09dee1461e43}{auto\+\_\+mot}} = 0
\item 
uint8\+\_\+t \mbox{\hyperlink{main_8c_ab13aaadd605aa27463297f4edebeb14b}{auto\+\_\+lidar}} = 0
\item 
uint16\+\_\+t \mbox{\hyperlink{main_8c_aa4951f1d11c92eb48a9886490d32ae93}{scan\+\_\+index}} = 0
\item 
uint32\+\_\+t \mbox{\hyperlink{main_8c_a7c70fc45e1d5f6181045180bff58b149}{turret\+\_\+move\+\_\+start}} = 0
\item 
uint16\+\_\+t \mbox{\hyperlink{main_8c_a943e6b8cd113aa2a9df8070046a55f3d}{min\+\_\+scan\+\_\+dist}} = 0x\+FFFF
\item 
uint16\+\_\+t \mbox{\hyperlink{main_8c_a6e54a03c7e9ef1412854f0e728c26649}{min\+\_\+scan\+\_\+index}} = 0
\item 
uint16\+\_\+t \mbox{\hyperlink{main_8c_aacd0e107eb88728e268e9374e0f89f83}{scan\+\_\+res}} = 20
\item 
int \mbox{\hyperlink{main_8c_a2e044faa4850a8748b4af2b82e7f9a99}{scan\+\_\+dist}} \mbox{[}20\mbox{]}
\item 
int \mbox{\hyperlink{main_8c_aa502b28b3c3a8d359c1de4c5b424981b}{scan\+\_\+amp}} \mbox{[}20\mbox{]}
\item 
uint8\+\_\+t \mbox{\hyperlink{main_8c_a84a9d93692a50eea6e1d36a7dcd3f7b2}{rx\+\_\+buffer}} \mbox{[}\mbox{\hyperlink{main_8c_a739a2a1a0047c98ac1b18ecd25dac092}{RX\+\_\+\+BUFFER\+\_\+\+SIZE}}\mbox{]}
\item 
uint8\+\_\+t \mbox{\hyperlink{main_8c_ac4b08f79fc99cb2c9c396b1d2be494bb}{rx\+\_\+index}} = 0
\item 
char \mbox{\hyperlink{main_8c_a58028125fa9a7629355ce57381239071}{msg\+\_\+int}} \mbox{[}64\mbox{]}
\item 
char \mbox{\hyperlink{main_8c_a698e9c2277f276efef4478a6c9cb069b}{msg\+\_\+main}} \mbox{[}64\mbox{]}
\item 
uint16\+\_\+t \mbox{\hyperlink{main_8c_a3f030bc6769aa19f45e30e3ab7cf244c}{servo\+\_\+angle}} = 140
\item 
uint16\+\_\+t \mbox{\hyperlink{main_8c_ad0429df5acd164397aa22c107c03bb5f}{servo\+\_\+step}} = 0
\item 
uint32\+\_\+t \mbox{\hyperlink{main_8c_a3a5348921762009e78b1b7d9e4102467}{servo\+\_\+step\+\_\+time}} = 0
\end{DoxyCompactItemize}

\doxysubsection{Detailed Description}
Application entry point for ping pong launcher project. 

This file initializes the STM32 peripherals, sets up the finite state machine (FSM), and starts the main control loop. The IMU is initialized and verified, but not actively used in the FSM during runtime.

Major functions\+:
\begin{DoxyItemize}
\item Setup clocks, timers, I2C, and UART
\item Initialize motors and servo
\item Run FSM in infinite loop
\item Provide IMU debug output for calibration and heading
\end{DoxyItemize}

\begin{DoxyAttention}{Attention}

\end{DoxyAttention}
Copyright (c) 2025 STMicroelectronics. All rights reserved.

This software is licensed under terms that can be found in the LICENSE file in the root directory of this software component. If no LICENSE file comes with this software, it is provided AS-\/\+IS. 

\label{doc-define-members}
\Hypertarget{main_8c_doc-define-members}
\doxysubsection{Macro Definition Documentation}
\Hypertarget{main_8c_a29671976836ee7a005ffc3b83cc9900a}\index{main.c@{main.c}!CPR\_TURRET@{CPR\_TURRET}}
\index{CPR\_TURRET@{CPR\_TURRET}!main.c@{main.c}}
\doxysubsubsection{\texorpdfstring{CPR\_TURRET}{CPR\_TURRET}}
{\footnotesize\ttfamily \label{main_8c_a29671976836ee7a005ffc3b83cc9900a} 
\#define CPR\+\_\+\+TURRET~3200}

\Hypertarget{main_8c_a739a2a1a0047c98ac1b18ecd25dac092}\index{main.c@{main.c}!RX\_BUFFER\_SIZE@{RX\_BUFFER\_SIZE}}
\index{RX\_BUFFER\_SIZE@{RX\_BUFFER\_SIZE}!main.c@{main.c}}
\doxysubsubsection{\texorpdfstring{RX\_BUFFER\_SIZE}{RX\_BUFFER\_SIZE}}
{\footnotesize\ttfamily \label{main_8c_a739a2a1a0047c98ac1b18ecd25dac092} 
\#define RX\+\_\+\+BUFFER\+\_\+\+SIZE~7}

\label{doc-enum-members}
\Hypertarget{main_8c_doc-enum-members}
\doxysubsection{Enumeration Type Documentation}
\Hypertarget{main_8c_ae2946618e700f814e6147195c808f4c8}\index{main.c@{main.c}!State\_t@{State\_t}}
\index{State\_t@{State\_t}!main.c@{main.c}}
\doxysubsubsection{\texorpdfstring{State\_t}{State\_t}}
{\footnotesize\ttfamily \label{main_8c_ae2946618e700f814e6147195c808f4c8} 
enum \mbox{\hyperlink{fsm_8h_ae2946618e700f814e6147195c808f4c8}{State\+\_\+t}}}

\begin{DoxyEnumFields}[2]{Enumerator}
\raisebox{\heightof{T}}[0pt][0pt]{\index{STATE\_0@{STATE\_0}!main.c@{main.c}}\index{main.c@{main.c}!STATE\_0@{STATE\_0}}}\Hypertarget{main_8c_ae2946618e700f814e6147195c808f4c8a830154cdb7fd42f54f25f9f428c2538d}\label{main_8c_ae2946618e700f814e6147195c808f4c8a830154cdb7fd42f54f25f9f428c2538d} 
STATE\+\_\+0&\\
\hline

\raisebox{\heightof{T}}[0pt][0pt]{\index{STATE\_1@{STATE\_1}!main.c@{main.c}}\index{main.c@{main.c}!STATE\_1@{STATE\_1}}}\Hypertarget{main_8c_ae2946618e700f814e6147195c808f4c8a3be8ff1b14d8f456ec4f53f6ce5790fa}\label{main_8c_ae2946618e700f814e6147195c808f4c8a3be8ff1b14d8f456ec4f53f6ce5790fa} 
STATE\+\_\+1&\\
\hline

\raisebox{\heightof{T}}[0pt][0pt]{\index{STATE\_2@{STATE\_2}!main.c@{main.c}}\index{main.c@{main.c}!STATE\_2@{STATE\_2}}}\Hypertarget{main_8c_ae2946618e700f814e6147195c808f4c8acd69fec890fc58a3ce12d157e80ab7cc}\label{main_8c_ae2946618e700f814e6147195c808f4c8acd69fec890fc58a3ce12d157e80ab7cc} 
STATE\+\_\+2&\\
\hline

\raisebox{\heightof{T}}[0pt][0pt]{\index{STATE\_3@{STATE\_3}!main.c@{main.c}}\index{main.c@{main.c}!STATE\_3@{STATE\_3}}}\Hypertarget{main_8c_ae2946618e700f814e6147195c808f4c8ac2afcd17617ae1ecba56029ff6c22e38}\label{main_8c_ae2946618e700f814e6147195c808f4c8ac2afcd17617ae1ecba56029ff6c22e38} 
STATE\+\_\+3&\\
\hline

\raisebox{\heightof{T}}[0pt][0pt]{\index{STATE\_4@{STATE\_4}!main.c@{main.c}}\index{main.c@{main.c}!STATE\_4@{STATE\_4}}}\Hypertarget{main_8c_ae2946618e700f814e6147195c808f4c8aa7e03e808984be120062b5e590333028}\label{main_8c_ae2946618e700f814e6147195c808f4c8aa7e03e808984be120062b5e590333028} 
STATE\+\_\+4&\\
\hline

\raisebox{\heightof{T}}[0pt][0pt]{\index{STATE\_5@{STATE\_5}!main.c@{main.c}}\index{main.c@{main.c}!STATE\_5@{STATE\_5}}}\Hypertarget{main_8c_ae2946618e700f814e6147195c808f4c8a247a852e037bd71e9c372e4cae5375a8}\label{main_8c_ae2946618e700f814e6147195c808f4c8a247a852e037bd71e9c372e4cae5375a8} 
STATE\+\_\+5&\\
\hline

\raisebox{\heightof{T}}[0pt][0pt]{\index{STATE\_6@{STATE\_6}!main.c@{main.c}}\index{main.c@{main.c}!STATE\_6@{STATE\_6}}}\Hypertarget{main_8c_ae2946618e700f814e6147195c808f4c8a1368a98786e7c54b0b1f078dedb08cb6}\label{main_8c_ae2946618e700f814e6147195c808f4c8a1368a98786e7c54b0b1f078dedb08cb6} 
STATE\+\_\+6&\\
\hline

\end{DoxyEnumFields}

\label{doc-func-members}
\Hypertarget{main_8c_doc-func-members}
\doxysubsection{Function Documentation}
\Hypertarget{main_8c_ade14a2f86085d70042e21b719d09b2fe}\index{main.c@{main.c}!dwt\_init@{dwt\_init}}
\index{dwt\_init@{dwt\_init}!main.c@{main.c}}
\doxysubsubsection{\texorpdfstring{dwt\_init()}{dwt\_init()}}
{\footnotesize\ttfamily \label{main_8c_ade14a2f86085d70042e21b719d09b2fe} 
void dwt\+\_\+init (\begin{DoxyParamCaption}\item[{void}]{}{}\end{DoxyParamCaption})}

\Hypertarget{main_8c_a1730ffe1e560465665eb47d9264826f9}\index{main.c@{main.c}!Error\_Handler@{Error\_Handler}}
\index{Error\_Handler@{Error\_Handler}!main.c@{main.c}}
\doxysubsubsection{\texorpdfstring{Error\_Handler()}{Error\_Handler()}}
{\footnotesize\ttfamily \label{main_8c_a1730ffe1e560465665eb47d9264826f9} 
void Error\+\_\+\+Handler (\begin{DoxyParamCaption}\item[{void}]{}{}\end{DoxyParamCaption})}

This function is executed in case of error occurrence. 

General error handler; enters infinite loop on fault.

\begin{DoxyRetVals}{Return values}
{\em None} & \\
\hline
\end{DoxyRetVals}
\Hypertarget{main_8c_ae494a9643f29b87d6d81e5264e60e57b}\index{main.c@{main.c}!HAL\_UART\_RxCpltCallback@{HAL\_UART\_RxCpltCallback}}
\index{HAL\_UART\_RxCpltCallback@{HAL\_UART\_RxCpltCallback}!main.c@{main.c}}
\doxysubsubsection{\texorpdfstring{HAL\_UART\_RxCpltCallback()}{HAL\_UART\_RxCpltCallback()}}
{\footnotesize\ttfamily \label{main_8c_ae494a9643f29b87d6d81e5264e60e57b} 
void HAL\+\_\+\+UART\+\_\+\+Rx\+Cplt\+Callback (\begin{DoxyParamCaption}\item[{UART\+\_\+\+Handle\+Type\+Def \texorpdfstring{$\ast$}{*}}]{huart}{}\end{DoxyParamCaption})}

\Hypertarget{main_8c_a840291bc02cba5474a4cb46a9b9566fe}\index{main.c@{main.c}!main@{main}}
\index{main@{main}!main.c@{main.c}}
\doxysubsubsection{\texorpdfstring{main()}{main()}}
{\footnotesize\ttfamily \label{main_8c_a840291bc02cba5474a4cb46a9b9566fe} 
int main (\begin{DoxyParamCaption}\item[{void}]{}{}\end{DoxyParamCaption})}

Main entry point — configures peripherals and enters control loop. 

\begin{DoxyRetVals}{Return values}
{\em int} & \\
\hline
\end{DoxyRetVals}
\Hypertarget{main_8c_a161515d302eceb8f79859465cadcdbc0}\index{main.c@{main.c}!servo\_pwm\_update@{servo\_pwm\_update}}
\index{servo\_pwm\_update@{servo\_pwm\_update}!main.c@{main.c}}
\doxysubsubsection{\texorpdfstring{servo\_pwm\_update()}{servo\_pwm\_update()}}
{\footnotesize\ttfamily \label{main_8c_a161515d302eceb8f79859465cadcdbc0} 
void servo\+\_\+pwm\+\_\+update (\begin{DoxyParamCaption}\item[{void}]{}{}\end{DoxyParamCaption})}

\Hypertarget{main_8c_a70af21c671abfcc773614a9a4f63d920}\index{main.c@{main.c}!SystemClock\_Config@{SystemClock\_Config}}
\index{SystemClock\_Config@{SystemClock\_Config}!main.c@{main.c}}
\doxysubsubsection{\texorpdfstring{SystemClock\_Config()}{SystemClock\_Config()}}
{\footnotesize\ttfamily \label{main_8c_a70af21c671abfcc773614a9a4f63d920} 
void System\+Clock\+\_\+\+Config (\begin{DoxyParamCaption}\item[{void}]{}{}\end{DoxyParamCaption})}

System Clock Configuration. 

\begin{DoxyRetVals}{Return values}
{\em None} & \\
\hline
\end{DoxyRetVals}
Configure the main internal regulator output voltage

Initializes the RCC Oscillators according to the specified parameters in the RCC\+\_\+\+Osc\+Init\+Type\+Def structure.

Initializes the CPU, AHB and APB buses clocks

\label{doc-var-members}
\Hypertarget{main_8c_doc-var-members}
\doxysubsection{Variable Documentation}
\Hypertarget{main_8c_ab13aaadd605aa27463297f4edebeb14b}\index{main.c@{main.c}!auto\_lidar@{auto\_lidar}}
\index{auto\_lidar@{auto\_lidar}!main.c@{main.c}}
\doxysubsubsection{\texorpdfstring{auto\_lidar}{auto\_lidar}}
{\footnotesize\ttfamily \label{main_8c_ab13aaadd605aa27463297f4edebeb14b} 
uint8\+\_\+t auto\+\_\+lidar = 0}

\Hypertarget{main_8c_a4d10e67794e6818e6b092b567855831c}\index{main.c@{main.c}!auto\_mode@{auto\_mode}}
\index{auto\_mode@{auto\_mode}!main.c@{main.c}}
\doxysubsubsection{\texorpdfstring{auto\_mode}{auto\_mode}}
{\footnotesize\ttfamily \label{main_8c_a4d10e67794e6818e6b092b567855831c} 
uint8\+\_\+t auto\+\_\+mode = 0}

\Hypertarget{main_8c_a080f3cf5f32d36259f3e09dee1461e43}\index{main.c@{main.c}!auto\_mot@{auto\_mot}}
\index{auto\_mot@{auto\_mot}!main.c@{main.c}}
\doxysubsubsection{\texorpdfstring{auto\_mot}{auto\_mot}}
{\footnotesize\ttfamily \label{main_8c_a080f3cf5f32d36259f3e09dee1461e43} 
uint8\+\_\+t auto\+\_\+mot = 0}

\Hypertarget{main_8c_a26e06bee38154c3e3480c6f6b723f059}\index{main.c@{main.c}!calib\_mode@{calib\_mode}}
\index{calib\_mode@{calib\_mode}!main.c@{main.c}}
\doxysubsubsection{\texorpdfstring{calib\_mode}{calib\_mode}}
{\footnotesize\ttfamily \label{main_8c_a26e06bee38154c3e3480c6f6b723f059} 
volatile uint8\+\_\+t calib\+\_\+mode = 0}

\Hypertarget{main_8c_aae419efef4a0d2b1a7ad68cb49a42389}\index{main.c@{main.c}!current\_state@{current\_state}}
\index{current\_state@{current\_state}!main.c@{main.c}}
\doxysubsubsection{\texorpdfstring{current\_state}{current\_state}}
{\footnotesize\ttfamily \label{main_8c_aae419efef4a0d2b1a7ad68cb49a42389} 
\mbox{\hyperlink{fsm_8h_ae2946618e700f814e6147195c808f4c8}{State\+\_\+t}} current\+\_\+state = \mbox{\hyperlink{fsm_8h_ae2946618e700f814e6147195c808f4c8a830154cdb7fd42f54f25f9f428c2538d}{STATE\+\_\+0}}}

\Hypertarget{main_8c_a7575fff8f1cf20db06571845911ac5ac}\index{main.c@{main.c}!duty\_flywheel1@{duty\_flywheel1}}
\index{duty\_flywheel1@{duty\_flywheel1}!main.c@{main.c}}
\doxysubsubsection{\texorpdfstring{duty\_flywheel1}{duty\_flywheel1}}
{\footnotesize\ttfamily \label{main_8c_a7575fff8f1cf20db06571845911ac5ac} 
int32\+\_\+t duty\+\_\+flywheel1 = 0}

\Hypertarget{main_8c_aaa2a7153eb2feab6c30fa192364f0a8a}\index{main.c@{main.c}!duty\_flywheel2@{duty\_flywheel2}}
\index{duty\_flywheel2@{duty\_flywheel2}!main.c@{main.c}}
\doxysubsubsection{\texorpdfstring{duty\_flywheel2}{duty\_flywheel2}}
{\footnotesize\ttfamily \label{main_8c_aaa2a7153eb2feab6c30fa192364f0a8a} 
int32\+\_\+t duty\+\_\+flywheel2 = 0}

\Hypertarget{main_8c_adbe25b24634a71fe4a900547f7e7d99e}\index{main.c@{main.c}!duty\_turret1@{duty\_turret1}}
\index{duty\_turret1@{duty\_turret1}!main.c@{main.c}}
\doxysubsubsection{\texorpdfstring{duty\_turret1}{duty\_turret1}}
{\footnotesize\ttfamily \label{main_8c_adbe25b24634a71fe4a900547f7e7d99e} 
int32\+\_\+t duty\+\_\+turret1 = 0}

\Hypertarget{main_8c_a698674f38793dd9795ca6b8bd25c2918}\index{main.c@{main.c}!duty\_turret2@{duty\_turret2}}
\index{duty\_turret2@{duty\_turret2}!main.c@{main.c}}
\doxysubsubsection{\texorpdfstring{duty\_turret2}{duty\_turret2}}
{\footnotesize\ttfamily \label{main_8c_a698674f38793dd9795ca6b8bd25c2918} 
int32\+\_\+t duty\+\_\+turret2 = 0}

\Hypertarget{main_8c_a6fa872f737d1eb3797b06ad86b910797}\index{main.c@{main.c}!flywheel1@{flywheel1}}
\index{flywheel1@{flywheel1}!main.c@{main.c}}
\doxysubsubsection{\texorpdfstring{flywheel1}{flywheel1}}
{\footnotesize\ttfamily \label{main_8c_a6fa872f737d1eb3797b06ad86b910797} 
\mbox{\hyperlink{structmotor__t}{motor\+\_\+t}} flywheel1}

{\bfseries Initial value\+:}
\begin{DoxyCode}{0}
\DoxyCodeLine{=\ \{}
\DoxyCodeLine{\ \ \ \ .htim\_forward\ =\ \&\mbox{\hyperlink{main_8c_a25fc663547539bc49fecc0011bd76ab5}{htim1}},\ .channel\_forward\ =\ TIM\_CHANNEL\_1,}
\DoxyCodeLine{\ \ \ \ .htim\_reverse\ =\ \&\mbox{\hyperlink{main_8c_a25fc663547539bc49fecc0011bd76ab5}{htim1}},\ .channel\_reverse\ =\ TIM\_CHANNEL\_4,}
\DoxyCodeLine{\ \ \ \ .duty\ =\ 0,\ .target\ =\ 0,\ .actual\ =\ 0}
\DoxyCodeLine{\}}

\end{DoxyCode}
\Hypertarget{main_8c_a1f60edf44bd9bde71ef7aae8d5863db2}\index{main.c@{main.c}!flywheel2@{flywheel2}}
\index{flywheel2@{flywheel2}!main.c@{main.c}}
\doxysubsubsection{\texorpdfstring{flywheel2}{flywheel2}}
{\footnotesize\ttfamily \label{main_8c_a1f60edf44bd9bde71ef7aae8d5863db2} 
\mbox{\hyperlink{structmotor__t}{motor\+\_\+t}} flywheel2}

{\bfseries Initial value\+:}
\begin{DoxyCode}{0}
\DoxyCodeLine{=\ \{}
\DoxyCodeLine{\ \ \ \ .htim\_forward\ =\ \&\mbox{\hyperlink{main_8c_a31f6f787777409af5ed0d131b52b7988}{htim9}},\ .channel\_forward\ =\ TIM\_CHANNEL\_1,}
\DoxyCodeLine{\ \ \ \ .htim\_reverse\ =\ \&\mbox{\hyperlink{main_8c_a31f6f787777409af5ed0d131b52b7988}{htim9}},\ .channel\_reverse\ =\ TIM\_CHANNEL\_2,}
\DoxyCodeLine{\ \ \ \ .duty\ =\ 0,\ .target\ =\ 0,\ .actual\ =\ 0}
\DoxyCodeLine{\}}

\end{DoxyCode}
\Hypertarget{main_8c_a22b804736f5648d52f639b2647d4ed13}\index{main.c@{main.c}!hadc1@{hadc1}}
\index{hadc1@{hadc1}!main.c@{main.c}}
\doxysubsubsection{\texorpdfstring{hadc1}{hadc1}}
{\footnotesize\ttfamily \label{main_8c_a22b804736f5648d52f639b2647d4ed13} 
ADC\+\_\+\+Handle\+Type\+Def hadc1}

\Hypertarget{main_8c_af7b2c26e44dadaaa798a5c3d82914ba7}\index{main.c@{main.c}!hi2c1@{hi2c1}}
\index{hi2c1@{hi2c1}!main.c@{main.c}}
\doxysubsubsection{\texorpdfstring{hi2c1}{hi2c1}}
{\footnotesize\ttfamily \label{main_8c_af7b2c26e44dadaaa798a5c3d82914ba7} 
I2\+C\+\_\+\+Handle\+Type\+Def hi2c1}

\Hypertarget{main_8c_ac379bcc152d860f08b1279fd3e232295}\index{main.c@{main.c}!hi2c2@{hi2c2}}
\index{hi2c2@{hi2c2}!main.c@{main.c}}
\doxysubsubsection{\texorpdfstring{hi2c2}{hi2c2}}
{\footnotesize\ttfamily \label{main_8c_ac379bcc152d860f08b1279fd3e232295} 
I2\+C\+\_\+\+Handle\+Type\+Def hi2c2}

\Hypertarget{main_8c_a25fc663547539bc49fecc0011bd76ab5}\index{main.c@{main.c}!htim1@{htim1}}
\index{htim1@{htim1}!main.c@{main.c}}
\doxysubsubsection{\texorpdfstring{htim1}{htim1}}
{\footnotesize\ttfamily \label{main_8c_a25fc663547539bc49fecc0011bd76ab5} 
TIM\+\_\+\+Handle\+Type\+Def htim1}

\Hypertarget{main_8c_a3c386e4f1937c518c1beccddef92045e}\index{main.c@{main.c}!htim10@{htim10}}
\index{htim10@{htim10}!main.c@{main.c}}
\doxysubsubsection{\texorpdfstring{htim10}{htim10}}
{\footnotesize\ttfamily \label{main_8c_a3c386e4f1937c518c1beccddef92045e} 
TIM\+\_\+\+Handle\+Type\+Def htim10}

\Hypertarget{main_8c_a2f22f985c4f33318fdcd4cc996623bf4}\index{main.c@{main.c}!htim11@{htim11}}
\index{htim11@{htim11}!main.c@{main.c}}
\doxysubsubsection{\texorpdfstring{htim11}{htim11}}
{\footnotesize\ttfamily \label{main_8c_a2f22f985c4f33318fdcd4cc996623bf4} 
TIM\+\_\+\+Handle\+Type\+Def htim11}

\Hypertarget{main_8c_a2c80fd5510e2990a59a5c90d745c716c}\index{main.c@{main.c}!htim2@{htim2}}
\index{htim2@{htim2}!main.c@{main.c}}
\doxysubsubsection{\texorpdfstring{htim2}{htim2}}
{\footnotesize\ttfamily \label{main_8c_a2c80fd5510e2990a59a5c90d745c716c} 
TIM\+\_\+\+Handle\+Type\+Def htim2}

\Hypertarget{main_8c_aac3d2c59ee0e3bbae1b99529a154eb62}\index{main.c@{main.c}!htim3@{htim3}}
\index{htim3@{htim3}!main.c@{main.c}}
\doxysubsubsection{\texorpdfstring{htim3}{htim3}}
{\footnotesize\ttfamily \label{main_8c_aac3d2c59ee0e3bbae1b99529a154eb62} 
TIM\+\_\+\+Handle\+Type\+Def htim3}

\Hypertarget{main_8c_a31f6f787777409af5ed0d131b52b7988}\index{main.c@{main.c}!htim9@{htim9}}
\index{htim9@{htim9}!main.c@{main.c}}
\doxysubsubsection{\texorpdfstring{htim9}{htim9}}
{\footnotesize\ttfamily \label{main_8c_a31f6f787777409af5ed0d131b52b7988} 
TIM\+\_\+\+Handle\+Type\+Def htim9}

\Hypertarget{main_8c_a2cf715bef37f7e8ef385a30974a5f0d5}\index{main.c@{main.c}!huart1@{huart1}}
\index{huart1@{huart1}!main.c@{main.c}}
\doxysubsubsection{\texorpdfstring{huart1}{huart1}}
{\footnotesize\ttfamily \label{main_8c_a2cf715bef37f7e8ef385a30974a5f0d5} 
UART\+\_\+\+Handle\+Type\+Def huart1}

UART interface used for IMU debug and user command output. 

\Hypertarget{main_8c_a79c01541f789e6b0e9da9bd118ef1681}\index{main.c@{main.c}!imu\_mode@{imu\_mode}}
\index{imu\_mode@{imu\_mode}!main.c@{main.c}}
\doxysubsubsection{\texorpdfstring{imu\_mode}{imu\_mode}}
{\footnotesize\ttfamily \label{main_8c_a79c01541f789e6b0e9da9bd118ef1681} 
volatile uint8\+\_\+t imu\+\_\+mode = 0}

\Hypertarget{main_8c_a5c1c771a6bca2a8939852e597c8054f6}\index{main.c@{main.c}!lidar\_buf@{lidar\_buf}}
\index{lidar\_buf@{lidar\_buf}!main.c@{main.c}}
\doxysubsubsection{\texorpdfstring{lidar\_buf}{lidar\_buf}}
{\footnotesize\ttfamily \label{main_8c_a5c1c771a6bca2a8939852e597c8054f6} 
uint8\+\_\+t lidar\+\_\+buf\mbox{[}4\mbox{]}}

\Hypertarget{main_8c_adce9412a27849ba591609b337dbc1369}\index{main.c@{main.c}!lidar\_mode@{lidar\_mode}}
\index{lidar\_mode@{lidar\_mode}!main.c@{main.c}}
\doxysubsubsection{\texorpdfstring{lidar\_mode}{lidar\_mode}}
{\footnotesize\ttfamily \label{main_8c_adce9412a27849ba591609b337dbc1369} 
volatile uint8\+\_\+t lidar\+\_\+mode = 0}

\Hypertarget{main_8c_a943e6b8cd113aa2a9df8070046a55f3d}\index{main.c@{main.c}!min\_scan\_dist@{min\_scan\_dist}}
\index{min\_scan\_dist@{min\_scan\_dist}!main.c@{main.c}}
\doxysubsubsection{\texorpdfstring{min\_scan\_dist}{min\_scan\_dist}}
{\footnotesize\ttfamily \label{main_8c_a943e6b8cd113aa2a9df8070046a55f3d} 
uint16\+\_\+t min\+\_\+scan\+\_\+dist = 0x\+FFFF}

\Hypertarget{main_8c_a6e54a03c7e9ef1412854f0e728c26649}\index{main.c@{main.c}!min\_scan\_index@{min\_scan\_index}}
\index{min\_scan\_index@{min\_scan\_index}!main.c@{main.c}}
\doxysubsubsection{\texorpdfstring{min\_scan\_index}{min\_scan\_index}}
{\footnotesize\ttfamily \label{main_8c_a6e54a03c7e9ef1412854f0e728c26649} 
uint16\+\_\+t min\+\_\+scan\+\_\+index = 0}

\Hypertarget{main_8c_a58028125fa9a7629355ce57381239071}\index{main.c@{main.c}!msg\_int@{msg\_int}}
\index{msg\_int@{msg\_int}!main.c@{main.c}}
\doxysubsubsection{\texorpdfstring{msg\_int}{msg\_int}}
{\footnotesize\ttfamily \label{main_8c_a58028125fa9a7629355ce57381239071} 
char msg\+\_\+int\mbox{[}64\mbox{]}}

\Hypertarget{main_8c_a698e9c2277f276efef4478a6c9cb069b}\index{main.c@{main.c}!msg\_main@{msg\_main}}
\index{msg\_main@{msg\_main}!main.c@{main.c}}
\doxysubsubsection{\texorpdfstring{msg\_main}{msg\_main}}
{\footnotesize\ttfamily \label{main_8c_a698e9c2277f276efef4478a6c9cb069b} 
char msg\+\_\+main\mbox{[}64\mbox{]}}

\Hypertarget{main_8c_a84a9d93692a50eea6e1d36a7dcd3f7b2}\index{main.c@{main.c}!rx\_buffer@{rx\_buffer}}
\index{rx\_buffer@{rx\_buffer}!main.c@{main.c}}
\doxysubsubsection{\texorpdfstring{rx\_buffer}{rx\_buffer}}
{\footnotesize\ttfamily \label{main_8c_a84a9d93692a50eea6e1d36a7dcd3f7b2} 
uint8\+\_\+t rx\+\_\+buffer\mbox{[}\mbox{\hyperlink{main_8c_a739a2a1a0047c98ac1b18ecd25dac092}{RX\+\_\+\+BUFFER\+\_\+\+SIZE}}\mbox{]}}

\Hypertarget{main_8c_ac4b08f79fc99cb2c9c396b1d2be494bb}\index{main.c@{main.c}!rx\_index@{rx\_index}}
\index{rx\_index@{rx\_index}!main.c@{main.c}}
\doxysubsubsection{\texorpdfstring{rx\_index}{rx\_index}}
{\footnotesize\ttfamily \label{main_8c_ac4b08f79fc99cb2c9c396b1d2be494bb} 
uint8\+\_\+t rx\+\_\+index = 0}

\Hypertarget{main_8c_aa502b28b3c3a8d359c1de4c5b424981b}\index{main.c@{main.c}!scan\_amp@{scan\_amp}}
\index{scan\_amp@{scan\_amp}!main.c@{main.c}}
\doxysubsubsection{\texorpdfstring{scan\_amp}{scan\_amp}}
{\footnotesize\ttfamily \label{main_8c_aa502b28b3c3a8d359c1de4c5b424981b} 
int scan\+\_\+amp\mbox{[}20\mbox{]}}

\Hypertarget{main_8c_a2e044faa4850a8748b4af2b82e7f9a99}\index{main.c@{main.c}!scan\_dist@{scan\_dist}}
\index{scan\_dist@{scan\_dist}!main.c@{main.c}}
\doxysubsubsection{\texorpdfstring{scan\_dist}{scan\_dist}}
{\footnotesize\ttfamily \label{main_8c_a2e044faa4850a8748b4af2b82e7f9a99} 
int scan\+\_\+dist\mbox{[}20\mbox{]}}

\Hypertarget{main_8c_aa4951f1d11c92eb48a9886490d32ae93}\index{main.c@{main.c}!scan\_index@{scan\_index}}
\index{scan\_index@{scan\_index}!main.c@{main.c}}
\doxysubsubsection{\texorpdfstring{scan\_index}{scan\_index}}
{\footnotesize\ttfamily \label{main_8c_aa4951f1d11c92eb48a9886490d32ae93} 
uint16\+\_\+t scan\+\_\+index = 0}

\Hypertarget{main_8c_aacd0e107eb88728e268e9374e0f89f83}\index{main.c@{main.c}!scan\_res@{scan\_res}}
\index{scan\_res@{scan\_res}!main.c@{main.c}}
\doxysubsubsection{\texorpdfstring{scan\_res}{scan\_res}}
{\footnotesize\ttfamily \label{main_8c_aacd0e107eb88728e268e9374e0f89f83} 
uint16\+\_\+t scan\+\_\+res = 20}

\Hypertarget{main_8c_a3f030bc6769aa19f45e30e3ab7cf244c}\index{main.c@{main.c}!servo\_angle@{servo\_angle}}
\index{servo\_angle@{servo\_angle}!main.c@{main.c}}
\doxysubsubsection{\texorpdfstring{servo\_angle}{servo\_angle}}
{\footnotesize\ttfamily \label{main_8c_a3f030bc6769aa19f45e30e3ab7cf244c} 
uint16\+\_\+t servo\+\_\+angle = 140}

\Hypertarget{main_8c_ad0429df5acd164397aa22c107c03bb5f}\index{main.c@{main.c}!servo\_step@{servo\_step}}
\index{servo\_step@{servo\_step}!main.c@{main.c}}
\doxysubsubsection{\texorpdfstring{servo\_step}{servo\_step}}
{\footnotesize\ttfamily \label{main_8c_ad0429df5acd164397aa22c107c03bb5f} 
uint16\+\_\+t servo\+\_\+step = 0}

\Hypertarget{main_8c_a3a5348921762009e78b1b7d9e4102467}\index{main.c@{main.c}!servo\_step\_time@{servo\_step\_time}}
\index{servo\_step\_time@{servo\_step\_time}!main.c@{main.c}}
\doxysubsubsection{\texorpdfstring{servo\_step\_time}{servo\_step\_time}}
{\footnotesize\ttfamily \label{main_8c_a3a5348921762009e78b1b7d9e4102467} 
uint32\+\_\+t servo\+\_\+step\+\_\+time = 0}

\Hypertarget{main_8c_a78c6167d8d0b21108c8e9a38f9ce05ff}\index{main.c@{main.c}!turret1@{turret1}}
\index{turret1@{turret1}!main.c@{main.c}}
\doxysubsubsection{\texorpdfstring{turret1}{turret1}}
{\footnotesize\ttfamily \label{main_8c_a78c6167d8d0b21108c8e9a38f9ce05ff} 
\mbox{\hyperlink{structmotor__t}{motor\+\_\+t}} turret1}

{\bfseries Initial value\+:}
\begin{DoxyCode}{0}
\DoxyCodeLine{=\ \{}
\DoxyCodeLine{\ \ \ \ .htim\_forward\ =\ \&\mbox{\hyperlink{main_8c_a25fc663547539bc49fecc0011bd76ab5}{htim1}},\ .channel\_forward\ =\ TIM\_CHANNEL\_2,}
\DoxyCodeLine{\ \ \ \ .htim\_reverse\ =\ \&\mbox{\hyperlink{main_8c_a25fc663547539bc49fecc0011bd76ab5}{htim1}},\ .channel\_reverse\ =\ TIM\_CHANNEL\_3,}
\DoxyCodeLine{\ \ \ \ .duty\ =\ 0,\ .target\ =\ 0,\ .actual\ =\ 0}
\DoxyCodeLine{\}}

\end{DoxyCode}
\Hypertarget{main_8c_a21a2e91d2dbeb89285478c49a0345f88}\index{main.c@{main.c}!turret1\_enc\_count@{turret1\_enc\_count}}
\index{turret1\_enc\_count@{turret1\_enc\_count}!main.c@{main.c}}
\doxysubsubsection{\texorpdfstring{turret1\_enc\_count}{turret1\_enc\_count}}
{\footnotesize\ttfamily \label{main_8c_a21a2e91d2dbeb89285478c49a0345f88} 
int32\+\_\+t turret1\+\_\+enc\+\_\+count = 0}

\Hypertarget{main_8c_a499be0edd8a3637fe08a286309cd5dbe}\index{main.c@{main.c}!turret1\_enc\_deg@{turret1\_enc\_deg}}
\index{turret1\_enc\_deg@{turret1\_enc\_deg}!main.c@{main.c}}
\doxysubsubsection{\texorpdfstring{turret1\_enc\_deg}{turret1\_enc\_deg}}
{\footnotesize\ttfamily \label{main_8c_a499be0edd8a3637fe08a286309cd5dbe} 
int32\+\_\+t turret1\+\_\+enc\+\_\+deg = 0}

\Hypertarget{main_8c_a1003878a23fa8103d73429ffcc76c37b}\index{main.c@{main.c}!turret1\_target@{turret1\_target}}
\index{turret1\_target@{turret1\_target}!main.c@{main.c}}
\doxysubsubsection{\texorpdfstring{turret1\_target}{turret1\_target}}
{\footnotesize\ttfamily \label{main_8c_a1003878a23fa8103d73429ffcc76c37b} 
int32\+\_\+t turret1\+\_\+target = 0}

\Hypertarget{main_8c_acfa9c01b03001c8c48f6885ef5fdd1e5}\index{main.c@{main.c}!turret2@{turret2}}
\index{turret2@{turret2}!main.c@{main.c}}
\doxysubsubsection{\texorpdfstring{turret2}{turret2}}
{\footnotesize\ttfamily \label{main_8c_acfa9c01b03001c8c48f6885ef5fdd1e5} 
\mbox{\hyperlink{structmotor__t}{motor\+\_\+t}} turret2}

{\bfseries Initial value\+:}
\begin{DoxyCode}{0}
\DoxyCodeLine{=\ \{}
\DoxyCodeLine{\ \ \ \ .htim\_forward\ =\ \&\mbox{\hyperlink{main_8c_a3c386e4f1937c518c1beccddef92045e}{htim10}},\ .channel\_forward\ =\ TIM\_CHANNEL\_1,}
\DoxyCodeLine{\ \ \ \ .htim\_reverse\ =\ \&\mbox{\hyperlink{main_8c_a2f22f985c4f33318fdcd4cc996623bf4}{htim11}},\ .channel\_reverse\ =\ TIM\_CHANNEL\_1,}
\DoxyCodeLine{\ \ \ \ .duty\ =\ 0,\ .target\ =\ 0,\ .actual\ =\ 0}
\DoxyCodeLine{\}}

\end{DoxyCode}
\Hypertarget{main_8c_a75ae1024ee7b8619b381e417164583f4}\index{main.c@{main.c}!turret2\_enc\_deg@{turret2\_enc\_deg}}
\index{turret2\_enc\_deg@{turret2\_enc\_deg}!main.c@{main.c}}
\doxysubsubsection{\texorpdfstring{turret2\_enc\_deg}{turret2\_enc\_deg}}
{\footnotesize\ttfamily \label{main_8c_a75ae1024ee7b8619b381e417164583f4} 
int32\+\_\+t turret2\+\_\+enc\+\_\+deg = 0}

\Hypertarget{main_8c_ae5d31aeb9915e39f86126cb0c2c377bb}\index{main.c@{main.c}!turret2\_enc\_pos@{turret2\_enc\_pos}}
\index{turret2\_enc\_pos@{turret2\_enc\_pos}!main.c@{main.c}}
\doxysubsubsection{\texorpdfstring{turret2\_enc\_pos}{turret2\_enc\_pos}}
{\footnotesize\ttfamily \label{main_8c_ae5d31aeb9915e39f86126cb0c2c377bb} 
int32\+\_\+t turret2\+\_\+enc\+\_\+pos = 0}

\Hypertarget{main_8c_a87c4df08862c1ffe52dbabbcf7cb400e}\index{main.c@{main.c}!turret2\_target@{turret2\_target}}
\index{turret2\_target@{turret2\_target}!main.c@{main.c}}
\doxysubsubsection{\texorpdfstring{turret2\_target}{turret2\_target}}
{\footnotesize\ttfamily \label{main_8c_a87c4df08862c1ffe52dbabbcf7cb400e} 
int32\+\_\+t turret2\+\_\+target = 0}

\Hypertarget{main_8c_a7c70fc45e1d5f6181045180bff58b149}\index{main.c@{main.c}!turret\_move\_start@{turret\_move\_start}}
\index{turret\_move\_start@{turret\_move\_start}!main.c@{main.c}}
\doxysubsubsection{\texorpdfstring{turret\_move\_start}{turret\_move\_start}}
{\footnotesize\ttfamily \label{main_8c_a7c70fc45e1d5f6181045180bff58b149} 
uint32\+\_\+t turret\+\_\+move\+\_\+start = 0}

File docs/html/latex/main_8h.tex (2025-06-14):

\doxysection{Core/\+Inc/main.h File Reference}
\hypertarget{main_8h}{}\label{main_8h}\index{Core/Inc/main.h@{Core/Inc/main.h}}

Main header for ping pong launcher project.  

{\ttfamily \#include "{}stm32f4xx\+\_\+hal.\+h"{}}\newline
\doxysubsubsection*{Functions}
\begin{DoxyCompactItemize}
\item 
void \mbox{\hyperlink{main_8h_ae70bce6c39d0b570a7523b86738cec4b}{HAL\+\_\+\+TIM\+\_\+\+Msp\+Post\+Init}} (TIM\+\_\+\+Handle\+Type\+Def \texorpdfstring{$\ast$}{*}htim)
\item 
void \mbox{\hyperlink{main_8h_a1730ffe1e560465665eb47d9264826f9}{Error\+\_\+\+Handler}} (void)
\begin{DoxyCompactList}\small\item\em General error handler; enters infinite loop on fault. \end{DoxyCompactList}\end{DoxyCompactItemize}
\doxysubsubsection*{Variables}
\begin{DoxyCompactItemize}
\item 
UART\+\_\+\+Handle\+Type\+Def \mbox{\hyperlink{main_8h_a2cf715bef37f7e8ef385a30974a5f0d5}{huart1}}
\begin{DoxyCompactList}\small\item\em UART interface used for IMU debug and user command output. \end{DoxyCompactList}\end{DoxyCompactItemize}

\doxysubsection{Detailed Description}
Main header for ping pong launcher project. 

This file contains global includes, definitions, and peripheral handles used throughout the autonomous ping pong ball launcher project.

Core modules include\+:
\begin{DoxyItemize}
\item FSM for control logic
\item IMU (BNO055) for orientation (demo only)
\item Motor control for turret and flywheel
\item Servo control for ball loading
\end{DoxyItemize}

The IMU is functional and reports heading data, but is not used in closed-\/loop control. This was left as future work.

\begin{DoxyAttention}{Attention}

\end{DoxyAttention}
Copyright (c) 2025 STMicroelectronics. All rights reserved.

This software is licensed under terms that can be found in the LICENSE file in the root directory of this software component. If no LICENSE file comes with this software, it is provided AS-\/\+IS. 

\label{doc-func-members}
\Hypertarget{main_8h_doc-func-members}
\doxysubsection{Function Documentation}
\Hypertarget{main_8h_a1730ffe1e560465665eb47d9264826f9}\index{main.h@{main.h}!Error\_Handler@{Error\_Handler}}
\index{Error\_Handler@{Error\_Handler}!main.h@{main.h}}
\doxysubsubsection{\texorpdfstring{Error\_Handler()}{Error\_Handler()}}
{\footnotesize\ttfamily \label{main_8h_a1730ffe1e560465665eb47d9264826f9} 
void Error\+\_\+\+Handler (\begin{DoxyParamCaption}\item[{void}]{}{}\end{DoxyParamCaption})}

General error handler; enters infinite loop on fault. 

General error handler; enters infinite loop on fault.

\begin{DoxyRetVals}{Return values}
{\em None} & \\
\hline
\end{DoxyRetVals}
\Hypertarget{main_8h_ae70bce6c39d0b570a7523b86738cec4b}\index{main.h@{main.h}!HAL\_TIM\_MspPostInit@{HAL\_TIM\_MspPostInit}}
\index{HAL\_TIM\_MspPostInit@{HAL\_TIM\_MspPostInit}!main.h@{main.h}}
\doxysubsubsection{\texorpdfstring{HAL\_TIM\_MspPostInit()}{HAL\_TIM\_MspPostInit()}}
{\footnotesize\ttfamily \label{main_8h_ae70bce6c39d0b570a7523b86738cec4b} 
void HAL\+\_\+\+TIM\+\_\+\+Msp\+Post\+Init (\begin{DoxyParamCaption}\item[{TIM\+\_\+\+Handle\+Type\+Def \texorpdfstring{$\ast$}{*}}]{htim}{}\end{DoxyParamCaption})}

TIM1 GPIO Configuration PB0 -\/-\/-\/-\/-\/-\/\texorpdfstring{$>$}{>} TIM1\+\_\+\+CH2N PB1 -\/-\/-\/-\/-\/-\/\texorpdfstring{$>$}{>} TIM1\+\_\+\+CH3N PA8 -\/-\/-\/-\/-\/-\/\texorpdfstring{$>$}{>} TIM1\+\_\+\+CH1 PA11 -\/-\/-\/-\/-\/-\/\texorpdfstring{$>$}{>} TIM1\+\_\+\+CH4

TIM9 GPIO Configuration PA2 -\/-\/-\/-\/-\/-\/\texorpdfstring{$>$}{>} TIM9\+\_\+\+CH1 PA3 -\/-\/-\/-\/-\/-\/\texorpdfstring{$>$}{>} TIM9\+\_\+\+CH2

TIM10 GPIO Configuration PB8 -\/-\/-\/-\/-\/-\/\texorpdfstring{$>$}{>} TIM10\+\_\+\+CH1

TIM11 GPIO Configuration PB9 -\/-\/-\/-\/-\/-\/\texorpdfstring{$>$}{>} TIM11\+\_\+\+CH1

\label{doc-var-members}
\Hypertarget{main_8h_doc-var-members}
\doxysubsection{Variable Documentation}
\Hypertarget{main_8h_a2cf715bef37f7e8ef385a30974a5f0d5}\index{main.h@{main.h}!huart1@{huart1}}
\index{huart1@{huart1}!main.h@{main.h}}
\doxysubsubsection{\texorpdfstring{huart1}{huart1}}
{\footnotesize\ttfamily \label{main_8h_a2cf715bef37f7e8ef385a30974a5f0d5} 
UART\+\_\+\+Handle\+Type\+Def huart1\hspace{0.3cm}{\ttfamily [extern]}}

UART interface used for IMU debug and user command output.

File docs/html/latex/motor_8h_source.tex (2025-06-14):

\doxysection{motor.\+h}
\hypertarget{motor_8h_source}{}\label{motor_8h_source}\index{Core/Inc/motor.h@{Core/Inc/motor.h}}
\mbox{\hyperlink{motor_8h}{Go to the documentation of this file.}}
\begin{DoxyCode}{0}
\DoxyCodeLine{00001\ }
\DoxyCodeLine{00012\ }
\DoxyCodeLine{00013\ \textcolor{preprocessor}{\#ifndef\ INC\_MOTOR\_H\_}}
\DoxyCodeLine{00014\ \textcolor{preprocessor}{\#define\ INC\_MOTOR\_H\_}}
\DoxyCodeLine{00015\ }
\DoxyCodeLine{00016\ \textcolor{preprocessor}{\#include\ <stdio.h>}}
\DoxyCodeLine{00017\ \textcolor{preprocessor}{\#include\ <stdint.h>}}
\DoxyCodeLine{00018\ \textcolor{preprocessor}{\#include\ "{}stm32f4xx\_hal.h"{}}}
\DoxyCodeLine{00019\ }
\DoxyCodeLine{00023\ \textcolor{keyword}{typedef}\ \textcolor{keyword}{struct\ }\{}
\DoxyCodeLine{00024\ \ \ \ \ TIM\_HandleTypeDef*\ \mbox{\hyperlink{structmotor__t_afae2dc04dec640da119145053d94fcb1}{htim\_forward}};}
\DoxyCodeLine{00025\ \ \ \ \ TIM\_HandleTypeDef*\ \mbox{\hyperlink{structmotor__t_a8bf10bb37d29314aadd521790b4d24e6}{htim\_reverse}};}
\DoxyCodeLine{00026\ \ \ \ \ uint32\_t\ \mbox{\hyperlink{structmotor__t_a10a73536377b630391241774ce730b99}{channel\_forward}};}
\DoxyCodeLine{00027\ \ \ \ \ uint32\_t\ \mbox{\hyperlink{structmotor__t_aa23dae8754ccfc8d772474e5edbdb6e6}{channel\_reverse}};}
\DoxyCodeLine{00028\ \ \ \ \ int32\_t\ \mbox{\hyperlink{structmotor__t_ab6a8993805fd7b50a32669337ca3a37a}{duty}};}
\DoxyCodeLine{00029\ \ \ \ \ int32\_t\ \mbox{\hyperlink{structmotor__t_ad696abb95bce893eae8836eb0b13f1f0}{target}};}
\DoxyCodeLine{00030\ \ \ \ \ int32\_t\ \mbox{\hyperlink{structmotor__t_a79a3f7d546c07fbab5eee73fbe2617c9}{actual}};}
\DoxyCodeLine{00031\ \}\ \mbox{\hyperlink{structmotor__t}{motor\_t}};}
\DoxyCodeLine{00032\ }
\DoxyCodeLine{00038\ \textcolor{keywordtype}{void}\ \mbox{\hyperlink{motor_8h_adcde1cd0aa97d50c0b1136c125b5ae10}{set\_duty}}(\mbox{\hyperlink{structmotor__t}{motor\_t}}*\ p\_mot,\ int32\_t\ duty);}
\DoxyCodeLine{00039\ }
\DoxyCodeLine{00046\ \textcolor{keywordtype}{void}\ \mbox{\hyperlink{motor_8h_a2c3f02a54893461ce371dfe296b020f7}{move\_to}}(\mbox{\hyperlink{structmotor__t}{motor\_t}}*\ p\_mot,\ int32\_t\ target,\ int32\_t\ actual);}
\DoxyCodeLine{00047\ }
\DoxyCodeLine{00052\ \textcolor{keywordtype}{void}\ \mbox{\hyperlink{motor_8h_a5f5eeae83ea21ae12701b0c0b78e691f}{disable}}(\mbox{\hyperlink{structmotor__t}{motor\_t}}*\ p\_mot);}
\DoxyCodeLine{00053\ }
\DoxyCodeLine{00058\ \textcolor{keywordtype}{void}\ \mbox{\hyperlink{motor_8h_a87e0de30f5044f896afc5ddaeff0f632}{enable}}(\mbox{\hyperlink{structmotor__t}{motor\_t}}*\ p\_mot);}
\DoxyCodeLine{00059\ }
\DoxyCodeLine{00060\ \textcolor{preprocessor}{\#endif\ }\textcolor{comment}{/*\ INC\_MOTOR\_H\_\ */}\textcolor{preprocessor}{}}

\end{DoxyCode}

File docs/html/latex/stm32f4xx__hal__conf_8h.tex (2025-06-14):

\doxysection{Core/\+Inc/stm32f4xx\+\_\+hal\+\_\+conf.h File Reference}
\hypertarget{stm32f4xx__hal__conf_8h}{}\label{stm32f4xx__hal__conf_8h}\index{Core/Inc/stm32f4xx\_hal\_conf.h@{Core/Inc/stm32f4xx\_hal\_conf.h}}
{\ttfamily \#include "{}stm32f4xx\+\_\+hal\+\_\+rcc.\+h"{}}\newline
{\ttfamily \#include "{}stm32f4xx\+\_\+hal\+\_\+gpio.\+h"{}}\newline
{\ttfamily \#include "{}stm32f4xx\+\_\+hal\+\_\+exti.\+h"{}}\newline
{\ttfamily \#include "{}stm32f4xx\+\_\+hal\+\_\+dma.\+h"{}}\newline
{\ttfamily \#include "{}stm32f4xx\+\_\+hal\+\_\+cortex.\+h"{}}\newline
{\ttfamily \#include "{}stm32f4xx\+\_\+hal\+\_\+adc.\+h"{}}\newline
{\ttfamily \#include "{}stm32f4xx\+\_\+hal\+\_\+flash.\+h"{}}\newline
{\ttfamily \#include "{}stm32f4xx\+\_\+hal\+\_\+i2c.\+h"{}}\newline
{\ttfamily \#include "{}stm32f4xx\+\_\+hal\+\_\+pwr.\+h"{}}\newline
{\ttfamily \#include "{}stm32f4xx\+\_\+hal\+\_\+tim.\+h"{}}\newline
{\ttfamily \#include "{}stm32f4xx\+\_\+hal\+\_\+uart.\+h"{}}\newline
\doxysubsubsection*{Macros}
\begin{DoxyCompactItemize}
\item 
\#define \mbox{\hyperlink{stm32f4xx__hal__conf_8h_a877ae99e8c47a609ea97c888912bf75f}{HAL\+\_\+\+MODULE\+\_\+\+ENABLED}}
\begin{DoxyCompactList}\small\item\em This is the list of modules to be used in the HAL driver. \end{DoxyCompactList}\item 
\#define \mbox{\hyperlink{stm32f4xx__hal__conf_8h_a476f1655c969ae57e89a74d98c75f43f}{HAL\+\_\+\+ADC\+\_\+\+MODULE\+\_\+\+ENABLED}}
\item 
\#define \mbox{\hyperlink{stm32f4xx__hal__conf_8h_a19999766418b0224871f732d800841c6}{HAL\+\_\+\+I2\+C\+\_\+\+MODULE\+\_\+\+ENABLED}}
\item 
\#define \mbox{\hyperlink{stm32f4xx__hal__conf_8h_a23382b8f04b3e6db2c59dfa1ef5ea4a2}{HAL\+\_\+\+TIM\+\_\+\+MODULE\+\_\+\+ENABLED}}
\item 
\#define \mbox{\hyperlink{stm32f4xx__hal__conf_8h_a167269406e73327b95c3bb7b9cfe6d89}{HAL\+\_\+\+UART\+\_\+\+MODULE\+\_\+\+ENABLED}}
\item 
\#define \mbox{\hyperlink{stm32f4xx__hal__conf_8h_a86165f80d6078719ee0715afe13febf5}{HAL\+\_\+\+GPIO\+\_\+\+MODULE\+\_\+\+ENABLED}}
\item 
\#define \mbox{\hyperlink{stm32f4xx__hal__conf_8h_aeb359e861d8a92c233c3229657dbcd74}{HAL\+\_\+\+EXTI\+\_\+\+MODULE\+\_\+\+ENABLED}}
\item 
\#define \mbox{\hyperlink{stm32f4xx__hal__conf_8h_a6552186102a1131b2849ac55a582945d}{HAL\+\_\+\+DMA\+\_\+\+MODULE\+\_\+\+ENABLED}}
\item 
\#define \mbox{\hyperlink{stm32f4xx__hal__conf_8h_ac3dd74314ed62ac8575e2f9f48b3ac48}{HAL\+\_\+\+RCC\+\_\+\+MODULE\+\_\+\+ENABLED}}
\item 
\#define \mbox{\hyperlink{stm32f4xx__hal__conf_8h_a7112575efe3740911f19a13e6b170fee}{HAL\+\_\+\+FLASH\+\_\+\+MODULE\+\_\+\+ENABLED}}
\item 
\#define \mbox{\hyperlink{stm32f4xx__hal__conf_8h_ab51923c3716977d7923f49cc9d081aa8}{HAL\+\_\+\+PWR\+\_\+\+MODULE\+\_\+\+ENABLED}}
\item 
\#define \mbox{\hyperlink{stm32f4xx__hal__conf_8h_aa9b5a3a425901e097de70092dbe31e0f}{HAL\+\_\+\+CORTEX\+\_\+\+MODULE\+\_\+\+ENABLED}}
\item 
\#define \mbox{\hyperlink{stm32f4xx__hal__conf_8h_aeafcff4f57440c60e64812dddd13e7cb}{HSE\+\_\+\+VALUE}}~16000000U
\begin{DoxyCompactList}\small\item\em Adjust the value of External High Speed oscillator (HSE) used in your application. This value is used by the RCC HAL module to compute the system frequency (when HSE is used as system clock source, directly or through the PLL). \end{DoxyCompactList}\item 
\#define \mbox{\hyperlink{stm32f4xx__hal__conf_8h_a68ecbc9b0a1a40a1ec9d18d5e9747c4f}{HSE\+\_\+\+STARTUP\+\_\+\+TIMEOUT}}~100U
\item 
\#define \mbox{\hyperlink{stm32f4xx__hal__conf_8h_aaa8c76e274d0f6dd2cefb5d0b17fbc37}{HSI\+\_\+\+VALUE}}~((uint32\+\_\+t)16000000U)
\begin{DoxyCompactList}\small\item\em Internal High Speed oscillator (HSI) value. This value is used by the RCC HAL module to compute the system frequency (when HSI is used as system clock source, directly or through the PLL). \end{DoxyCompactList}\item 
\#define \mbox{\hyperlink{stm32f4xx__hal__conf_8h_a4872023e65449c0506aac3ea6bec99e9}{LSI\+\_\+\+VALUE}}~32000U
\begin{DoxyCompactList}\small\item\em Internal Low Speed oscillator (LSI) value. \end{DoxyCompactList}\item 
\#define \mbox{\hyperlink{stm32f4xx__hal__conf_8h_a7bbb9d19e5189a6ccd0fb6fa6177d20d}{LSE\+\_\+\+VALUE}}~32768U
\begin{DoxyCompactList}\small\item\em External Low Speed oscillator (LSE) value. \end{DoxyCompactList}\item 
\#define \mbox{\hyperlink{stm32f4xx__hal__conf_8h_a85e6fc812dc26f7161a04be2568a5462}{LSE\+\_\+\+STARTUP\+\_\+\+TIMEOUT}}~5000U
\item 
\#define \mbox{\hyperlink{stm32f4xx__hal__conf_8h_a8c47c935e91e70569098b41718558648}{EXTERNAL\+\_\+\+CLOCK\+\_\+\+VALUE}}~12288000U
\begin{DoxyCompactList}\small\item\em External clock source for I2S peripheral This value is used by the I2S HAL module to compute the I2S clock source frequency, this source is inserted directly through I2\+S\+\_\+\+CKIN pad. \end{DoxyCompactList}\item 
\#define \mbox{\hyperlink{stm32f4xx__hal__conf_8h_aae550dad9f96d52cfce5e539adadbbb4}{VDD\+\_\+\+VALUE}}~3300U
\begin{DoxyCompactList}\small\item\em This is the HAL system configuration section. \end{DoxyCompactList}\item 
\#define \mbox{\hyperlink{stm32f4xx__hal__conf_8h_ae27809d4959b9fd5b5d974e3e1c77d2e}{TICK\+\_\+\+INT\+\_\+\+PRIORITY}}~15U
\item 
\#define \mbox{\hyperlink{stm32f4xx__hal__conf_8h_ad048ac737242c2c2cb9f4a72953d10ce}{USE\+\_\+\+RTOS}}~0U
\item 
\#define \mbox{\hyperlink{stm32f4xx__hal__conf_8h_a13fc0d5e7bb925385c0cc0772ba6a391}{PREFETCH\+\_\+\+ENABLE}}~1U
\item 
\#define \mbox{\hyperlink{stm32f4xx__hal__conf_8h_a3379989d46599c7e19a43f42e9145a4a}{INSTRUCTION\+\_\+\+CACHE\+\_\+\+ENABLE}}~1U
\item 
\#define \mbox{\hyperlink{stm32f4xx__hal__conf_8h_a5b4c32a40cf49b06c0d761e385949a6b}{DATA\+\_\+\+CACHE\+\_\+\+ENABLE}}~1U
\item 
\#define \mbox{\hyperlink{stm32f4xx__hal__conf_8h_acc33abd5393affd16cc4a1397839dfe4}{USE\+\_\+\+HAL\+\_\+\+ADC\+\_\+\+REGISTER\+\_\+\+CALLBACKS}}~0U /\texorpdfstring{$\ast$}{*} ADC register callback disabled       \texorpdfstring{$\ast$}{*}/
\item 
\#define \mbox{\hyperlink{stm32f4xx__hal__conf_8h_a7f6bf06dfbf91fd866a9d62ab54d0e81}{USE\+\_\+\+HAL\+\_\+\+CAN\+\_\+\+REGISTER\+\_\+\+CALLBACKS}}~0U /\texorpdfstring{$\ast$}{*} CAN register callback disabled       \texorpdfstring{$\ast$}{*}/
\item 
\#define \mbox{\hyperlink{stm32f4xx__hal__conf_8h_a4b1a233981ef5d96551ea1f08d1a7ea8}{USE\+\_\+\+HAL\+\_\+\+CEC\+\_\+\+REGISTER\+\_\+\+CALLBACKS}}~0U /\texorpdfstring{$\ast$}{*} CEC register callback disabled       \texorpdfstring{$\ast$}{*}/
\item 
\#define \mbox{\hyperlink{stm32f4xx__hal__conf_8h_aab15bfcb9198618bda3d7e914193b466}{USE\+\_\+\+HAL\+\_\+\+CRYP\+\_\+\+REGISTER\+\_\+\+CALLBACKS}}~0U /\texorpdfstring{$\ast$}{*} CRYP register callback disabled      \texorpdfstring{$\ast$}{*}/
\item 
\#define \mbox{\hyperlink{stm32f4xx__hal__conf_8h_af9580ae862dcc02cee7822030c48d6b8}{USE\+\_\+\+HAL\+\_\+\+DAC\+\_\+\+REGISTER\+\_\+\+CALLBACKS}}~0U /\texorpdfstring{$\ast$}{*} DAC register callback disabled       \texorpdfstring{$\ast$}{*}/
\item 
\#define \mbox{\hyperlink{stm32f4xx__hal__conf_8h_a64a4d06cebee4009f08652637fbf161d}{USE\+\_\+\+HAL\+\_\+\+DCMI\+\_\+\+REGISTER\+\_\+\+CALLBACKS}}~0U /\texorpdfstring{$\ast$}{*} DCMI register callback disabled      \texorpdfstring{$\ast$}{*}/
\item 
\#define \mbox{\hyperlink{stm32f4xx__hal__conf_8h_a86882c5f53554e458434c836812093db}{USE\+\_\+\+HAL\+\_\+\+DFSDM\+\_\+\+REGISTER\+\_\+\+CALLBACKS}}~0U /\texorpdfstring{$\ast$}{*} DFSDM register callback disabled     \texorpdfstring{$\ast$}{*}/
\item 
\#define \mbox{\hyperlink{stm32f4xx__hal__conf_8h_ad3fd64734f71ef9c872f38dd0d0b8cb0}{USE\+\_\+\+HAL\+\_\+\+DMA2\+D\+\_\+\+REGISTER\+\_\+\+CALLBACKS}}~0U /\texorpdfstring{$\ast$}{*} DMA2D register callback disabled     \texorpdfstring{$\ast$}{*}/
\item 
\#define \mbox{\hyperlink{stm32f4xx__hal__conf_8h_a6c2182c3202253ba1a70c7d25122013c}{USE\+\_\+\+HAL\+\_\+\+DSI\+\_\+\+REGISTER\+\_\+\+CALLBACKS}}~0U /\texorpdfstring{$\ast$}{*} DSI register callback disabled       \texorpdfstring{$\ast$}{*}/
\item 
\#define \mbox{\hyperlink{stm32f4xx__hal__conf_8h_aa24a8d7886d3a497a868d5bf2417bfdf}{USE\+\_\+\+HAL\+\_\+\+ETH\+\_\+\+REGISTER\+\_\+\+CALLBACKS}}~0U /\texorpdfstring{$\ast$}{*} ETH register callback disabled       \texorpdfstring{$\ast$}{*}/
\item 
\#define \mbox{\hyperlink{stm32f4xx__hal__conf_8h_a0390418ff6315463b6ef161c63a69d43}{USE\+\_\+\+HAL\+\_\+\+HASH\+\_\+\+REGISTER\+\_\+\+CALLBACKS}}~0U /\texorpdfstring{$\ast$}{*} HASH register callback disabled      \texorpdfstring{$\ast$}{*}/
\item 
\#define \mbox{\hyperlink{stm32f4xx__hal__conf_8h_a560b53001fb58138f7da15dbda8f58a6}{USE\+\_\+\+HAL\+\_\+\+HCD\+\_\+\+REGISTER\+\_\+\+CALLBACKS}}~0U /\texorpdfstring{$\ast$}{*} HCD register callback disabled       \texorpdfstring{$\ast$}{*}/
\item 
\#define \mbox{\hyperlink{stm32f4xx__hal__conf_8h_a99be773f7f62b6277d1c87658e085725}{USE\+\_\+\+HAL\+\_\+\+I2\+C\+\_\+\+REGISTER\+\_\+\+CALLBACKS}}~0U /\texorpdfstring{$\ast$}{*} I2C register callback disabled       \texorpdfstring{$\ast$}{*}/
\item 
\#define \mbox{\hyperlink{stm32f4xx__hal__conf_8h_a940b1da88a7c3b2be040ff8bd05d2e7c}{USE\+\_\+\+HAL\+\_\+\+FMPI2\+C\+\_\+\+REGISTER\+\_\+\+CALLBACKS}}~0U /\texorpdfstring{$\ast$}{*} FMPI2C register callback disabled    \texorpdfstring{$\ast$}{*}/
\item 
\#define \mbox{\hyperlink{stm32f4xx__hal__conf_8h_a46f8aba8b355db501b426e3a82620e47}{USE\+\_\+\+HAL\+\_\+\+FMPSMBUS\+\_\+\+REGISTER\+\_\+\+CALLBACKS}}~0U /\texorpdfstring{$\ast$}{*} FMPSMBUS register callback disabled  \texorpdfstring{$\ast$}{*}/
\item 
\#define \mbox{\hyperlink{stm32f4xx__hal__conf_8h_a1bdc791c35b20c7188b3d74fd6c30ebf}{USE\+\_\+\+HAL\+\_\+\+I2\+S\+\_\+\+REGISTER\+\_\+\+CALLBACKS}}~0U /\texorpdfstring{$\ast$}{*} I2S register callback disabled       \texorpdfstring{$\ast$}{*}/
\item 
\#define \mbox{\hyperlink{stm32f4xx__hal__conf_8h_a4a459bcaa046998e6939fc66b0831e96}{USE\+\_\+\+HAL\+\_\+\+IRDA\+\_\+\+REGISTER\+\_\+\+CALLBACKS}}~0U /\texorpdfstring{$\ast$}{*} IRDA register callback disabled      \texorpdfstring{$\ast$}{*}/
\item 
\#define \mbox{\hyperlink{stm32f4xx__hal__conf_8h_a5b148dcae2bf8f576fc69a349794df4c}{USE\+\_\+\+HAL\+\_\+\+LPTIM\+\_\+\+REGISTER\+\_\+\+CALLBACKS}}~0U /\texorpdfstring{$\ast$}{*} LPTIM register callback disabled     \texorpdfstring{$\ast$}{*}/
\item 
\#define \mbox{\hyperlink{stm32f4xx__hal__conf_8h_a2297103b8900168640d1225072361808}{USE\+\_\+\+HAL\+\_\+\+LTDC\+\_\+\+REGISTER\+\_\+\+CALLBACKS}}~0U /\texorpdfstring{$\ast$}{*} LTDC register callback disabled      \texorpdfstring{$\ast$}{*}/
\item 
\#define \mbox{\hyperlink{stm32f4xx__hal__conf_8h_ae595e885d73a91a83fbdc20f7affcd42}{USE\+\_\+\+HAL\+\_\+\+MMC\+\_\+\+REGISTER\+\_\+\+CALLBACKS}}~0U /\texorpdfstring{$\ast$}{*} MMC register callback disabled       \texorpdfstring{$\ast$}{*}/
\item 
\#define \mbox{\hyperlink{stm32f4xx__hal__conf_8h_a80498b459859528918535b88fed54b28}{USE\+\_\+\+HAL\+\_\+\+NAND\+\_\+\+REGISTER\+\_\+\+CALLBACKS}}~0U /\texorpdfstring{$\ast$}{*} NAND register callback disabled      \texorpdfstring{$\ast$}{*}/
\item 
\#define \mbox{\hyperlink{stm32f4xx__hal__conf_8h_a7b38c01bd6621f3da5993d71eb5ff42e}{USE\+\_\+\+HAL\+\_\+\+NOR\+\_\+\+REGISTER\+\_\+\+CALLBACKS}}~0U /\texorpdfstring{$\ast$}{*} NOR register callback disabled       \texorpdfstring{$\ast$}{*}/
\item 
\#define \mbox{\hyperlink{stm32f4xx__hal__conf_8h_a15d7e736835fdf5b02fe42913329a5ce}{USE\+\_\+\+HAL\+\_\+\+PCCARD\+\_\+\+REGISTER\+\_\+\+CALLBACKS}}~0U /\texorpdfstring{$\ast$}{*} PCCARD register callback disabled    \texorpdfstring{$\ast$}{*}/
\item 
\#define \mbox{\hyperlink{stm32f4xx__hal__conf_8h_afd18c04aa4a4a54446df8083be875a00}{USE\+\_\+\+HAL\+\_\+\+PCD\+\_\+\+REGISTER\+\_\+\+CALLBACKS}}~0U /\texorpdfstring{$\ast$}{*} PCD register callback disabled       \texorpdfstring{$\ast$}{*}/
\item 
\#define \mbox{\hyperlink{stm32f4xx__hal__conf_8h_a95cbcf73c2ae3aea55fb62502ed224a2}{USE\+\_\+\+HAL\+\_\+\+QSPI\+\_\+\+REGISTER\+\_\+\+CALLBACKS}}~0U /\texorpdfstring{$\ast$}{*} QSPI register callback disabled      \texorpdfstring{$\ast$}{*}/
\item 
\#define \mbox{\hyperlink{stm32f4xx__hal__conf_8h_a9b01c64d19f0d4839b7da08bd61c7ff7}{USE\+\_\+\+HAL\+\_\+\+RNG\+\_\+\+REGISTER\+\_\+\+CALLBACKS}}~0U /\texorpdfstring{$\ast$}{*} RNG register callback disabled       \texorpdfstring{$\ast$}{*}/
\item 
\#define \mbox{\hyperlink{stm32f4xx__hal__conf_8h_a54badbcdb096ce802d2eed981cbbc31a}{USE\+\_\+\+HAL\+\_\+\+RTC\+\_\+\+REGISTER\+\_\+\+CALLBACKS}}~0U /\texorpdfstring{$\ast$}{*} RTC register callback disabled       \texorpdfstring{$\ast$}{*}/
\item 
\#define \mbox{\hyperlink{stm32f4xx__hal__conf_8h_a0e2ac47c259fc72ef188c0406a2af803}{USE\+\_\+\+HAL\+\_\+\+SAI\+\_\+\+REGISTER\+\_\+\+CALLBACKS}}~0U /\texorpdfstring{$\ast$}{*} SAI register callback disabled       \texorpdfstring{$\ast$}{*}/
\item 
\#define \mbox{\hyperlink{stm32f4xx__hal__conf_8h_acccbc010792c242ce6aae30b7c6f40df}{USE\+\_\+\+HAL\+\_\+\+SD\+\_\+\+REGISTER\+\_\+\+CALLBACKS}}~0U /\texorpdfstring{$\ast$}{*} SD register callback disabled        \texorpdfstring{$\ast$}{*}/
\item 
\#define \mbox{\hyperlink{stm32f4xx__hal__conf_8h_a43bb2335641440326db0f05526c1bff9}{USE\+\_\+\+HAL\+\_\+\+SMARTCARD\+\_\+\+REGISTER\+\_\+\+CALLBACKS}}~0U /\texorpdfstring{$\ast$}{*} SMARTCARD register callback disabled \texorpdfstring{$\ast$}{*}/
\item 
\#define \mbox{\hyperlink{stm32f4xx__hal__conf_8h_a0732f81973e1744fe9eec6d2f451faff}{USE\+\_\+\+HAL\+\_\+\+SDRAM\+\_\+\+REGISTER\+\_\+\+CALLBACKS}}~0U /\texorpdfstring{$\ast$}{*} SDRAM register callback disabled     \texorpdfstring{$\ast$}{*}/
\item 
\#define \mbox{\hyperlink{stm32f4xx__hal__conf_8h_a5c7c04d57c22f5301f1ea589abc6f35f}{USE\+\_\+\+HAL\+\_\+\+SRAM\+\_\+\+REGISTER\+\_\+\+CALLBACKS}}~0U /\texorpdfstring{$\ast$}{*} SRAM register callback disabled      \texorpdfstring{$\ast$}{*}/
\item 
\#define \mbox{\hyperlink{stm32f4xx__hal__conf_8h_a91d326d554db420a247bd4eec1951961}{USE\+\_\+\+HAL\+\_\+\+SPDIFRX\+\_\+\+REGISTER\+\_\+\+CALLBACKS}}~0U /\texorpdfstring{$\ast$}{*} SPDIFRX register callback disabled   \texorpdfstring{$\ast$}{*}/
\item 
\#define \mbox{\hyperlink{stm32f4xx__hal__conf_8h_a74cae3ff25398b4a06a579a7164a8518}{USE\+\_\+\+HAL\+\_\+\+SMBUS\+\_\+\+REGISTER\+\_\+\+CALLBACKS}}~0U /\texorpdfstring{$\ast$}{*} SMBUS register callback disabled     \texorpdfstring{$\ast$}{*}/
\item 
\#define \mbox{\hyperlink{stm32f4xx__hal__conf_8h_a8d8be2d7e4ed5bfc7b64f60ba604c749}{USE\+\_\+\+HAL\+\_\+\+SPI\+\_\+\+REGISTER\+\_\+\+CALLBACKS}}~0U /\texorpdfstring{$\ast$}{*} SPI register callback disabled       \texorpdfstring{$\ast$}{*}/
\item 
\#define \mbox{\hyperlink{stm32f4xx__hal__conf_8h_a5ef4d67cd7630f6e2e67d17370fbffdb}{USE\+\_\+\+HAL\+\_\+\+TIM\+\_\+\+REGISTER\+\_\+\+CALLBACKS}}~0U /\texorpdfstring{$\ast$}{*} TIM register callback disabled       \texorpdfstring{$\ast$}{*}/
\item 
\#define \mbox{\hyperlink{stm32f4xx__hal__conf_8h_a68c6c7c633e6cb378824020ef00a5701}{USE\+\_\+\+HAL\+\_\+\+UART\+\_\+\+REGISTER\+\_\+\+CALLBACKS}}~0U /\texorpdfstring{$\ast$}{*} UART register callback disabled      \texorpdfstring{$\ast$}{*}/
\item 
\#define \mbox{\hyperlink{stm32f4xx__hal__conf_8h_ac79983d623c7f760c5077618a453561b}{USE\+\_\+\+HAL\+\_\+\+USART\+\_\+\+REGISTER\+\_\+\+CALLBACKS}}~0U /\texorpdfstring{$\ast$}{*} USART register callback disabled     \texorpdfstring{$\ast$}{*}/
\item 
\#define \mbox{\hyperlink{stm32f4xx__hal__conf_8h_a6879802837c27d8761d8a8fdab626891}{USE\+\_\+\+HAL\+\_\+\+WWDG\+\_\+\+REGISTER\+\_\+\+CALLBACKS}}~0U /\texorpdfstring{$\ast$}{*} WWDG register callback disabled      \texorpdfstring{$\ast$}{*}/
\item 
\#define \mbox{\hyperlink{stm32f4xx__hal__conf_8h_ab84a2e15d360e2644ada09641513a941}{MAC\+\_\+\+ADDR0}}~2U
\begin{DoxyCompactList}\small\item\em Uncomment the line below to expanse the "{}assert\+\_\+param"{} macro in the HAL drivers code. \end{DoxyCompactList}\item 
\#define \mbox{\hyperlink{stm32f4xx__hal__conf_8h_a8d14266d76690c530bee01e7e5bb4099}{MAC\+\_\+\+ADDR1}}~0U
\item 
\#define \mbox{\hyperlink{stm32f4xx__hal__conf_8h_a6c5df15bec1d305ed033ad9a85ec803d}{MAC\+\_\+\+ADDR2}}~0U
\item 
\#define \mbox{\hyperlink{stm32f4xx__hal__conf_8h_a08a36ede83ae67498aecf54676be8fc8}{MAC\+\_\+\+ADDR3}}~0U
\item 
\#define \mbox{\hyperlink{stm32f4xx__hal__conf_8h_a41e5cb0b39ad74f0aafb83dbcecf9006}{MAC\+\_\+\+ADDR4}}~0U
\item 
\#define \mbox{\hyperlink{stm32f4xx__hal__conf_8h_a3bcc92663c42ec434f527847bbc4abc1}{MAC\+\_\+\+ADDR5}}~0U
\item 
\#define \mbox{\hyperlink{stm32f4xx__hal__conf_8h_a0cdaf687f7a7f2dba570d5a722990786}{ETH\+\_\+\+RX\+\_\+\+BUF\+\_\+\+SIZE}}~ETH\+\_\+\+MAX\+\_\+\+PACKET\+\_\+\+SIZE /\texorpdfstring{$\ast$}{*} buffer size for receive               \texorpdfstring{$\ast$}{*}/
\item 
\#define \mbox{\hyperlink{stm32f4xx__hal__conf_8h_af83956dfc1b135c3c92ac409758b6cf4}{ETH\+\_\+\+TX\+\_\+\+BUF\+\_\+\+SIZE}}~ETH\+\_\+\+MAX\+\_\+\+PACKET\+\_\+\+SIZE /\texorpdfstring{$\ast$}{*} buffer size for transmit              \texorpdfstring{$\ast$}{*}/
\item 
\#define \mbox{\hyperlink{stm32f4xx__hal__conf_8h_a62b0f224fa9c4f2e5574c9e52526f751}{ETH\+\_\+\+RXBUFNB}}~4U       /\texorpdfstring{$\ast$}{*} 4 Rx buffers of size \mbox{\hyperlink{stm32f4xx__hal__conf_8h_a0cdaf687f7a7f2dba570d5a722990786}{ETH\+\_\+\+RX\+\_\+\+BUF\+\_\+\+SIZE}}  \texorpdfstring{$\ast$}{*}/
\item 
\#define \mbox{\hyperlink{stm32f4xx__hal__conf_8h_a4ad07ad8fa6f8639ab8ef362390d86c7}{ETH\+\_\+\+TXBUFNB}}~4U       /\texorpdfstring{$\ast$}{*} 4 Tx buffers of size \mbox{\hyperlink{stm32f4xx__hal__conf_8h_af83956dfc1b135c3c92ac409758b6cf4}{ETH\+\_\+\+TX\+\_\+\+BUF\+\_\+\+SIZE}}  \texorpdfstring{$\ast$}{*}/
\item 
\#define \mbox{\hyperlink{stm32f4xx__hal__conf_8h_a25f014091aaba92bdd9d95d0b2f00503}{DP83848\+\_\+\+PHY\+\_\+\+ADDRESS}}
\item 
\#define \mbox{\hyperlink{stm32f4xx__hal__conf_8h_a0ede6087f7b71403bcddb5d3a8f47ff4}{PHY\+\_\+\+RESET\+\_\+\+DELAY}}~0x000000\+FFU
\item 
\#define \mbox{\hyperlink{stm32f4xx__hal__conf_8h_abba7114255a2a41b81fdcb2a3702c270}{PHY\+\_\+\+CONFIG\+\_\+\+DELAY}}~0x00000\+FFFU
\item 
\#define \mbox{\hyperlink{stm32f4xx__hal__conf_8h_a9d356ada86535630c403690bef0fb887}{PHY\+\_\+\+READ\+\_\+\+TO}}~0x0000\+FFFFU
\item 
\#define \mbox{\hyperlink{stm32f4xx__hal__conf_8h_a474bf13e28d09b667e41b151140ee39d}{PHY\+\_\+\+WRITE\+\_\+\+TO}}~0x0000\+FFFFU
\item 
\#define \mbox{\hyperlink{stm32f4xx__hal__conf_8h_a8abe1a40c71e68881ec669d59f513fdb}{PHY\+\_\+\+BCR}}~((uint16\+\_\+t)0x0000U)
\item 
\#define \mbox{\hyperlink{stm32f4xx__hal__conf_8h_a4b8f2c29a9e74412395e1b1809666838}{PHY\+\_\+\+BSR}}~((uint16\+\_\+t)0x0001U)
\item 
\#define \mbox{\hyperlink{stm32f4xx__hal__conf_8h_a6f5048620b3dde8583f7f1118e9de187}{PHY\+\_\+\+RESET}}~((uint16\+\_\+t)0x8000U)
\item 
\#define \mbox{\hyperlink{stm32f4xx__hal__conf_8h_a7833d885caa7e29abbebfb90a4b96f86}{PHY\+\_\+\+LOOPBACK}}~((uint16\+\_\+t)0x4000U)
\item 
\#define \mbox{\hyperlink{stm32f4xx__hal__conf_8h_a5729771244f68779fc694ba819cd60a5}{PHY\+\_\+\+FULLDUPLEX\+\_\+100M}}~((uint16\+\_\+t)0x2100U)
\item 
\#define \mbox{\hyperlink{stm32f4xx__hal__conf_8h_a1ac901a4ad405241d90a5c10104b8986}{PHY\+\_\+\+HALFDUPLEX\+\_\+100M}}~((uint16\+\_\+t)0x2000U)
\item 
\#define \mbox{\hyperlink{stm32f4xx__hal__conf_8h_a6b6254fd3dacbf1578a9d8058cd86373}{PHY\+\_\+\+FULLDUPLEX\+\_\+10M}}~((uint16\+\_\+t)0x0100U)
\item 
\#define \mbox{\hyperlink{stm32f4xx__hal__conf_8h_a4fa7ca6faf60ee074576ebb6103f8dd4}{PHY\+\_\+\+HALFDUPLEX\+\_\+10M}}~((uint16\+\_\+t)0x0000U)
\item 
\#define \mbox{\hyperlink{stm32f4xx__hal__conf_8h_a9b7f5c8f71047ee449f21562d26b1b43}{PHY\+\_\+\+AUTONEGOTIATION}}~((uint16\+\_\+t)0x1000U)
\item 
\#define \mbox{\hyperlink{stm32f4xx__hal__conf_8h_a66c4b69bd08dc25b6730365d3ff740c9}{PHY\+\_\+\+RESTART\+\_\+\+AUTONEGOTIATION}}~((uint16\+\_\+t)0x0200U)
\item 
\#define \mbox{\hyperlink{stm32f4xx__hal__conf_8h_aa0b1e6d4a23470fc1ac4f9222b51f8a0}{PHY\+\_\+\+POWERDOWN}}~((uint16\+\_\+t)0x0800U)
\item 
\#define \mbox{\hyperlink{stm32f4xx__hal__conf_8h_a7d5233295134a385866eb5bdafe2162b}{PHY\+\_\+\+ISOLATE}}~((uint16\+\_\+t)0x0400U)
\item 
\#define \mbox{\hyperlink{stm32f4xx__hal__conf_8h_a36c4dbd5f6df1f5eaefa010929ef9773}{PHY\+\_\+\+AUTONEGO\+\_\+\+COMPLETE}}~((uint16\+\_\+t)0x0020U)
\item 
\#define \mbox{\hyperlink{stm32f4xx__hal__conf_8h_ace209074499dbef0b97300da5bd7c707}{PHY\+\_\+\+LINKED\+\_\+\+STATUS}}~((uint16\+\_\+t)0x0004U)
\item 
\#define \mbox{\hyperlink{stm32f4xx__hal__conf_8h_a057b4d3fb66548d65c291a5b41611be2}{PHY\+\_\+\+JABBER\+\_\+\+DETECTION}}~((uint16\+\_\+t)0x0002U)
\item 
\#define \mbox{\hyperlink{stm32f4xx__hal__conf_8h_a32b55e84d27cf298a77f54b133cd1acc}{PHY\+\_\+\+SR}}~((uint16\+\_\+t))
\item 
\#define \mbox{\hyperlink{stm32f4xx__hal__conf_8h_a74c081bc55e9ff96bf229f44e96c6155}{PHY\+\_\+\+SPEED\+\_\+\+STATUS}}~((uint16\+\_\+t))
\item 
\#define \mbox{\hyperlink{stm32f4xx__hal__conf_8h_ab928f45585242fde1a8d81a2d9ed22d0}{PHY\+\_\+\+DUPLEX\+\_\+\+STATUS}}~((uint16\+\_\+t))
\item 
\#define \mbox{\hyperlink{stm32f4xx__hal__conf_8h_a4c6fab687afc7ba4469b1b2d34472358}{USE\+\_\+\+SPI\+\_\+\+CRC}}~0U
\item 
\#define \mbox{\hyperlink{stm32f4xx__hal__conf_8h_a631dea7b230e600555f979c62af1de21}{assert\+\_\+param}}(expr)
\begin{DoxyCompactList}\small\item\em Include module\textquotesingle{}s header file. \end{DoxyCompactList}\end{DoxyCompactItemize}

\label{doc-define-members}
\Hypertarget{stm32f4xx__hal__conf_8h_doc-define-members}
\doxysubsection{Macro Definition Documentation}
\Hypertarget{stm32f4xx__hal__conf_8h_a631dea7b230e600555f979c62af1de21}\index{stm32f4xx\_hal\_conf.h@{stm32f4xx\_hal\_conf.h}!assert\_param@{assert\_param}}
\index{assert\_param@{assert\_param}!stm32f4xx\_hal\_conf.h@{stm32f4xx\_hal\_conf.h}}
\doxysubsubsection{\texorpdfstring{assert\_param}{assert\_param}}
{\footnotesize\ttfamily \label{stm32f4xx__hal__conf_8h_a631dea7b230e600555f979c62af1de21} 
\#define assert\+\_\+param(\begin{DoxyParamCaption}\item[{}]{expr}{}\end{DoxyParamCaption})}

{\bfseries Value\+:}
\begin{DoxyCode}{0}
\DoxyCodeLine{((void)0U)}

\end{DoxyCode}

Include module\textquotesingle{}s header file. 

\Hypertarget{stm32f4xx__hal__conf_8h_a5b4c32a40cf49b06c0d761e385949a6b}\index{stm32f4xx\_hal\_conf.h@{stm32f4xx\_hal\_conf.h}!DATA\_CACHE\_ENABLE@{DATA\_CACHE\_ENABLE}}
\index{DATA\_CACHE\_ENABLE@{DATA\_CACHE\_ENABLE}!stm32f4xx\_hal\_conf.h@{stm32f4xx\_hal\_conf.h}}
\doxysubsubsection{\texorpdfstring{DATA\_CACHE\_ENABLE}{DATA\_CACHE\_ENABLE}}
{\footnotesize\ttfamily \label{stm32f4xx__hal__conf_8h_a5b4c32a40cf49b06c0d761e385949a6b} 
\#define DATA\+\_\+\+CACHE\+\_\+\+ENABLE~1U}

\Hypertarget{stm32f4xx__hal__conf_8h_a25f014091aaba92bdd9d95d0b2f00503}\index{stm32f4xx\_hal\_conf.h@{stm32f4xx\_hal\_conf.h}!DP83848\_PHY\_ADDRESS@{DP83848\_PHY\_ADDRESS}}
\index{DP83848\_PHY\_ADDRESS@{DP83848\_PHY\_ADDRESS}!stm32f4xx\_hal\_conf.h@{stm32f4xx\_hal\_conf.h}}
\doxysubsubsection{\texorpdfstring{DP83848\_PHY\_ADDRESS}{DP83848\_PHY\_ADDRESS}}
{\footnotesize\ttfamily \label{stm32f4xx__hal__conf_8h_a25f014091aaba92bdd9d95d0b2f00503} 
\#define DP83848\+\_\+\+PHY\+\_\+\+ADDRESS}

\Hypertarget{stm32f4xx__hal__conf_8h_a0cdaf687f7a7f2dba570d5a722990786}\index{stm32f4xx\_hal\_conf.h@{stm32f4xx\_hal\_conf.h}!ETH\_RX\_BUF\_SIZE@{ETH\_RX\_BUF\_SIZE}}
\index{ETH\_RX\_BUF\_SIZE@{ETH\_RX\_BUF\_SIZE}!stm32f4xx\_hal\_conf.h@{stm32f4xx\_hal\_conf.h}}
\doxysubsubsection{\texorpdfstring{ETH\_RX\_BUF\_SIZE}{ETH\_RX\_BUF\_SIZE}}
{\footnotesize\ttfamily \label{stm32f4xx__hal__conf_8h_a0cdaf687f7a7f2dba570d5a722990786} 
\#define ETH\+\_\+\+RX\+\_\+\+BUF\+\_\+\+SIZE~ETH\+\_\+\+MAX\+\_\+\+PACKET\+\_\+\+SIZE /\texorpdfstring{$\ast$}{*} buffer size for receive               \texorpdfstring{$\ast$}{*}/}

\Hypertarget{stm32f4xx__hal__conf_8h_a62b0f224fa9c4f2e5574c9e52526f751}\index{stm32f4xx\_hal\_conf.h@{stm32f4xx\_hal\_conf.h}!ETH\_RXBUFNB@{ETH\_RXBUFNB}}
\index{ETH\_RXBUFNB@{ETH\_RXBUFNB}!stm32f4xx\_hal\_conf.h@{stm32f4xx\_hal\_conf.h}}
\doxysubsubsection{\texorpdfstring{ETH\_RXBUFNB}{ETH\_RXBUFNB}}
{\footnotesize\ttfamily \label{stm32f4xx__hal__conf_8h_a62b0f224fa9c4f2e5574c9e52526f751} 
\#define ETH\+\_\+\+RXBUFNB~4U       /\texorpdfstring{$\ast$}{*} 4 Rx buffers of size \mbox{\hyperlink{stm32f4xx__hal__conf_8h_a0cdaf687f7a7f2dba570d5a722990786}{ETH\+\_\+\+RX\+\_\+\+BUF\+\_\+\+SIZE}}  \texorpdfstring{$\ast$}{*}/}
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

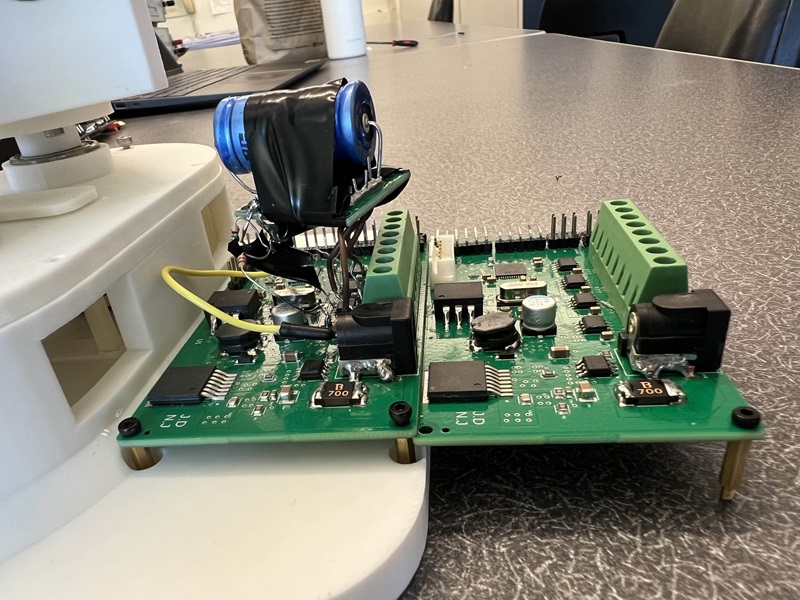
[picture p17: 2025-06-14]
Images/before&afterpcb.jpg

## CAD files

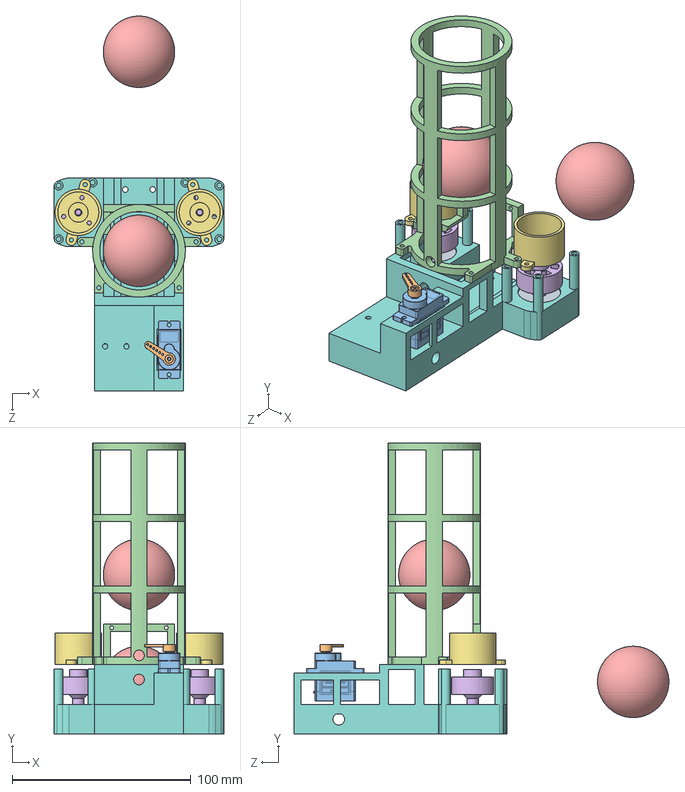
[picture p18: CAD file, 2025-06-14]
CAD_MECHANICAL_SYSTEM/LauncherA.SLDASM
95.0 x 163.0 x 209.9 mm
launcher
DCXMount x 2
Flywheel x 2
PPBall x 2
Magazine
SG90 - Micro Servo 9g - Tower Pro.1
SG90 - Micro Servo 9g - Tower Pro.2
7-Bearing x 2

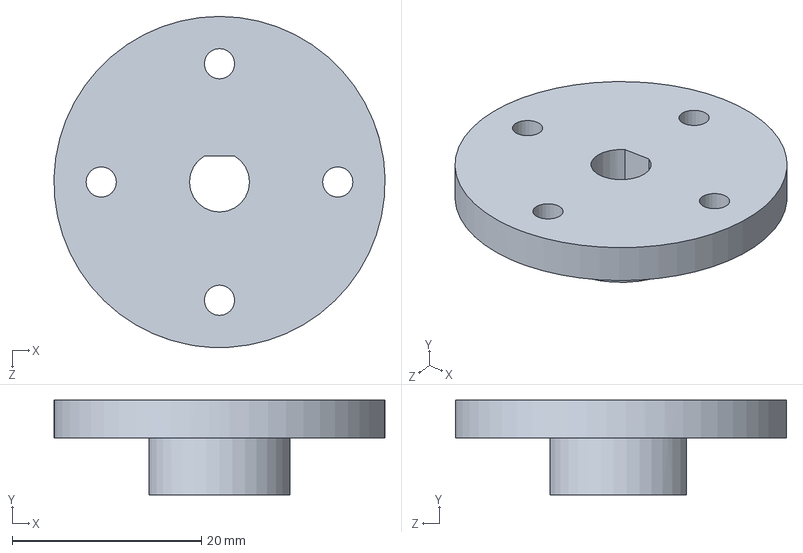
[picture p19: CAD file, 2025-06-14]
CAD_MECHANICAL_SYSTEM/VAssemblyMount.SLDPRT
35.0 x 10.0 x 35.0 mm

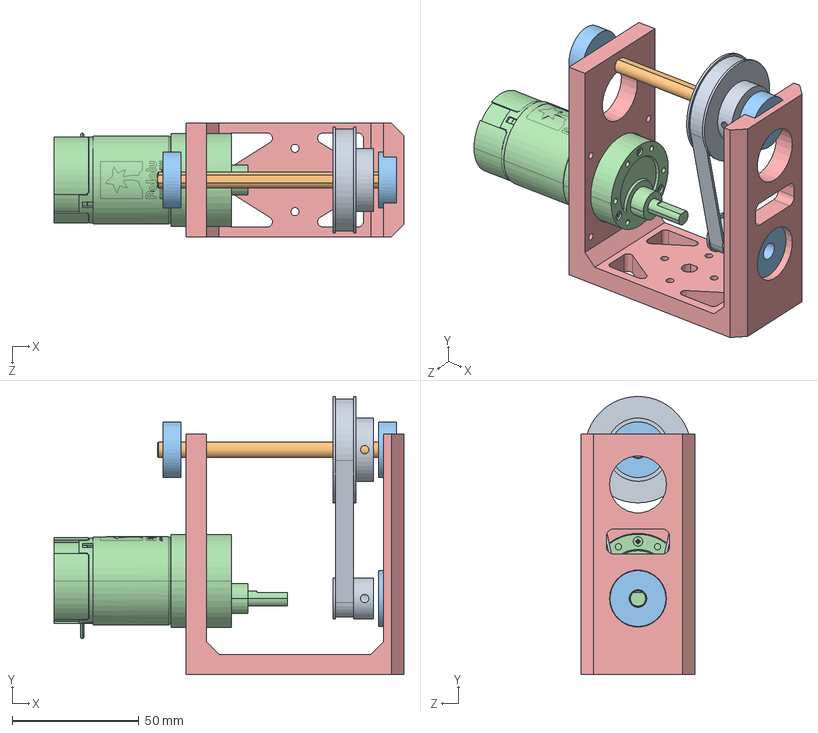
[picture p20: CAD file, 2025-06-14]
CAD_MECHANICAL_SYSTEM/VertJoint.SLDASM
138.1 x 109.7 x 45.0 mm
Vertgear
37d-gearmotor-50-70-encoder
7-Bearing x 3
VShaft2
Pulleys

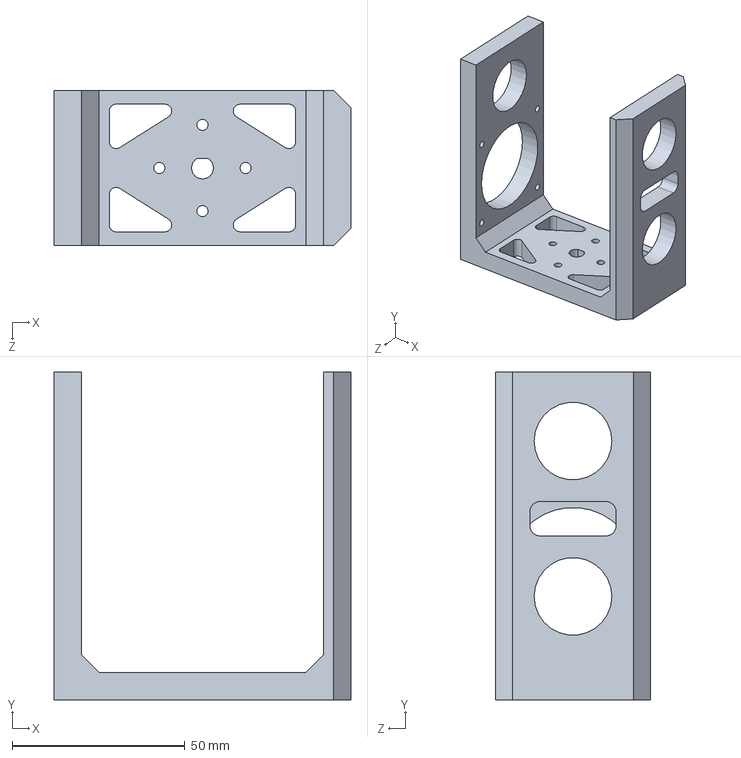
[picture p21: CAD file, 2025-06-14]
CAD_MECHANICAL_SYSTEM/Vertgear.SLDPRT
86.0 x 95.0 x 45.0 mm

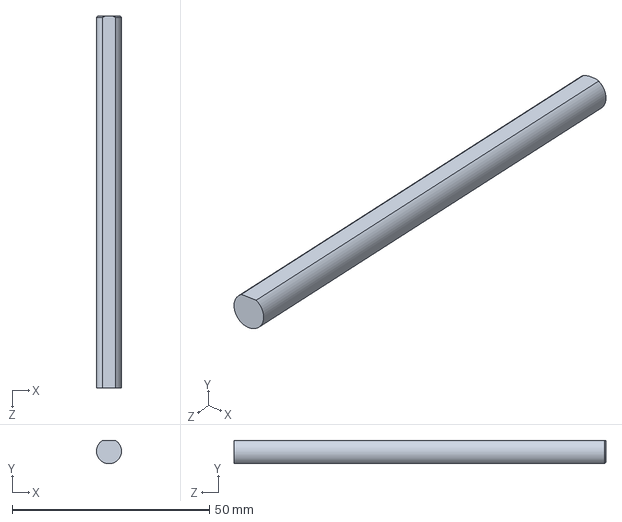
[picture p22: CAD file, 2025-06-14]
CAD_MECHANICAL_SYSTEM/VShaft2.SLDPRT
6.34 x 5.92 x 94.2 mm

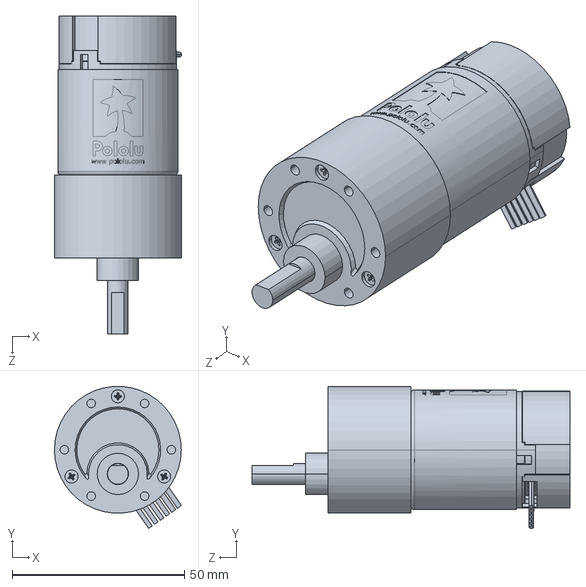
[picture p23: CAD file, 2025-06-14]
CAD_MECHANICAL_SYSTEM/37d-gearmotor-50-70-encoder.SLDPRT
36.9 x 41.2 x 92.1 mm

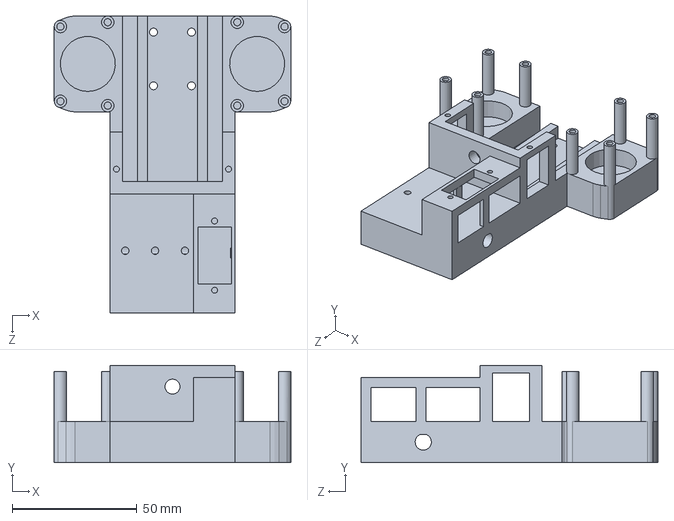
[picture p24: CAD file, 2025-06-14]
CAD_MECHANICAL_SYSTEM/launcher.SLDPRT
95.0 x 39.0 x 119.2 mm

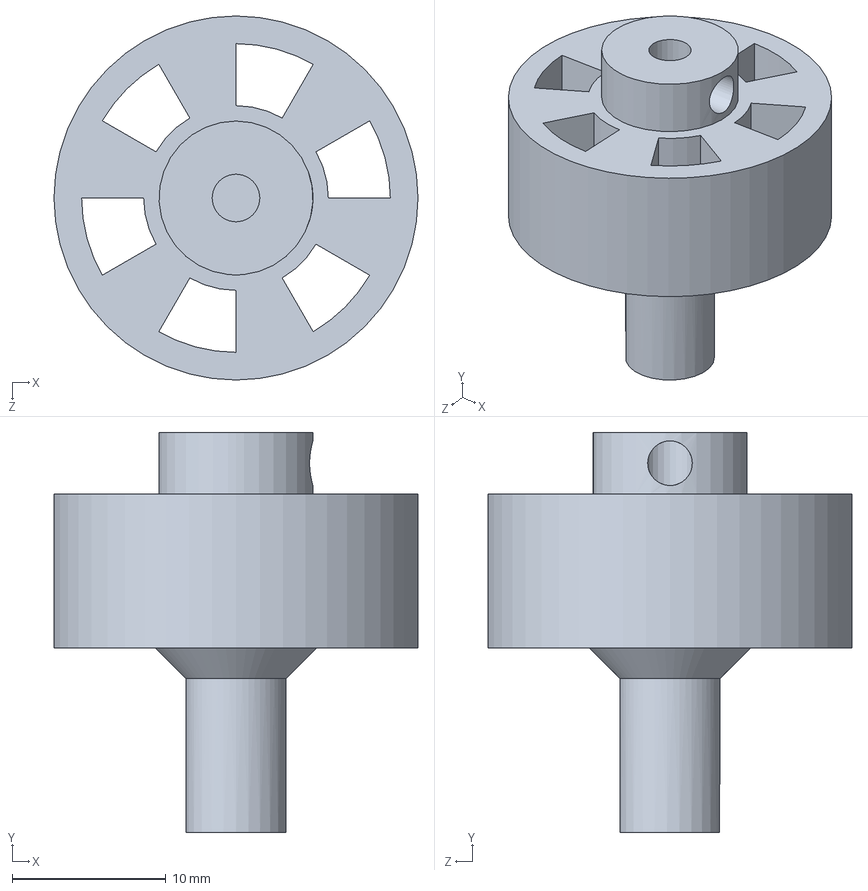
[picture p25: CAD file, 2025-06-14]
CAD_MECHANICAL_SYSTEM/Flywheel.SLDPRT
23.6 x 26.0 x 23.6 mm

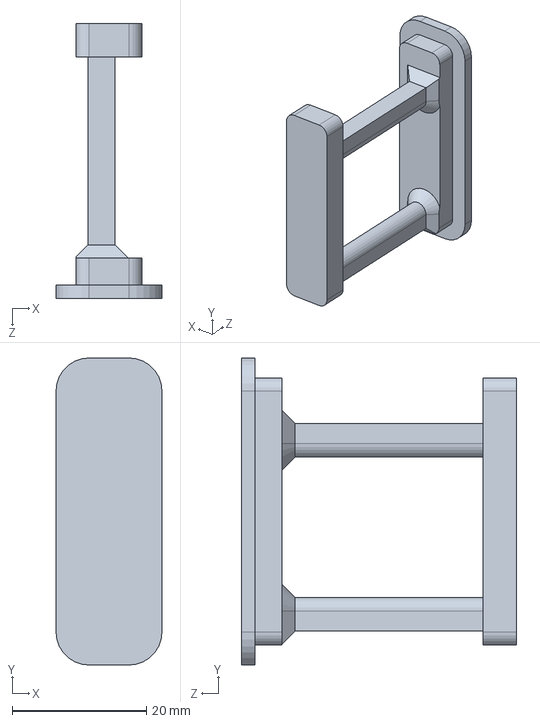
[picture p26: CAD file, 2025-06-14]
CAD_MECHANICAL_SYSTEM/BaseTensioner.SLDPRT
15.8 x 45.8 x 41.0 mm

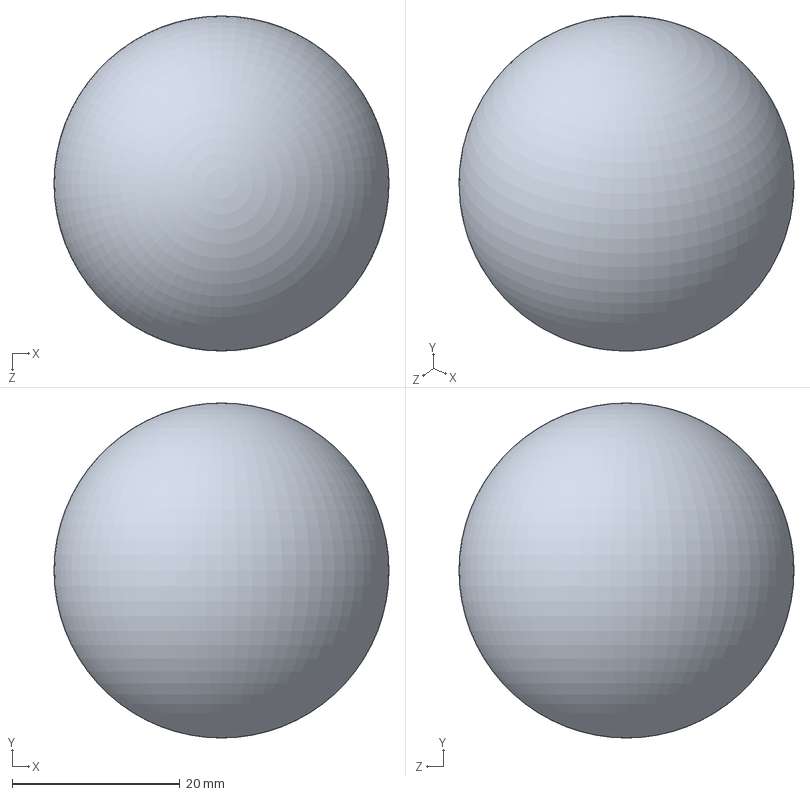
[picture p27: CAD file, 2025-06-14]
CAD_MECHANICAL_SYSTEM/PPBall.SLDPRT
40.0 x 40.0 x 40.0 mm

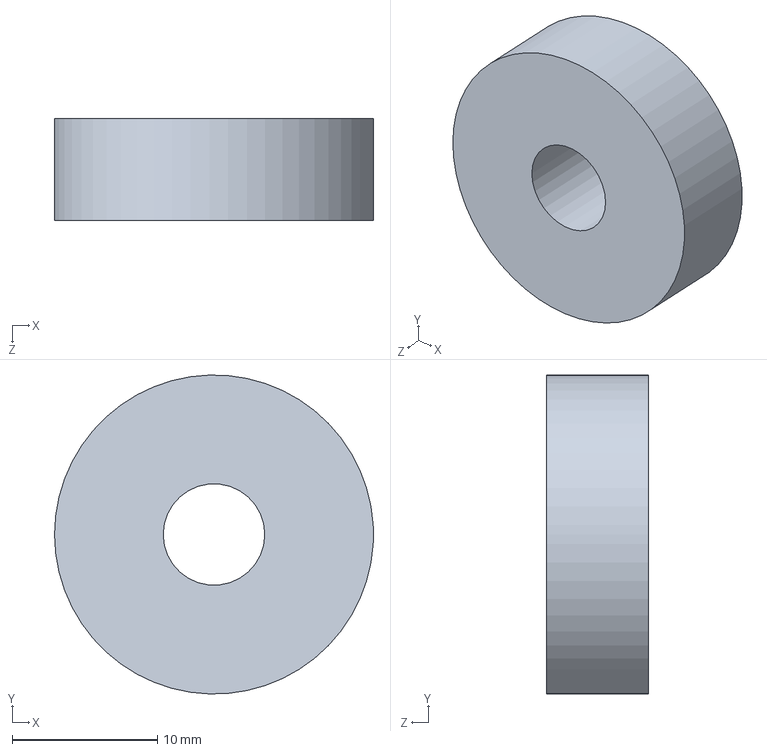
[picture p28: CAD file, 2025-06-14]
CAD_MECHANICAL_SYSTEM/7-Bearing.SLDPRT
22.0 x 22.0 x 7.00 mm

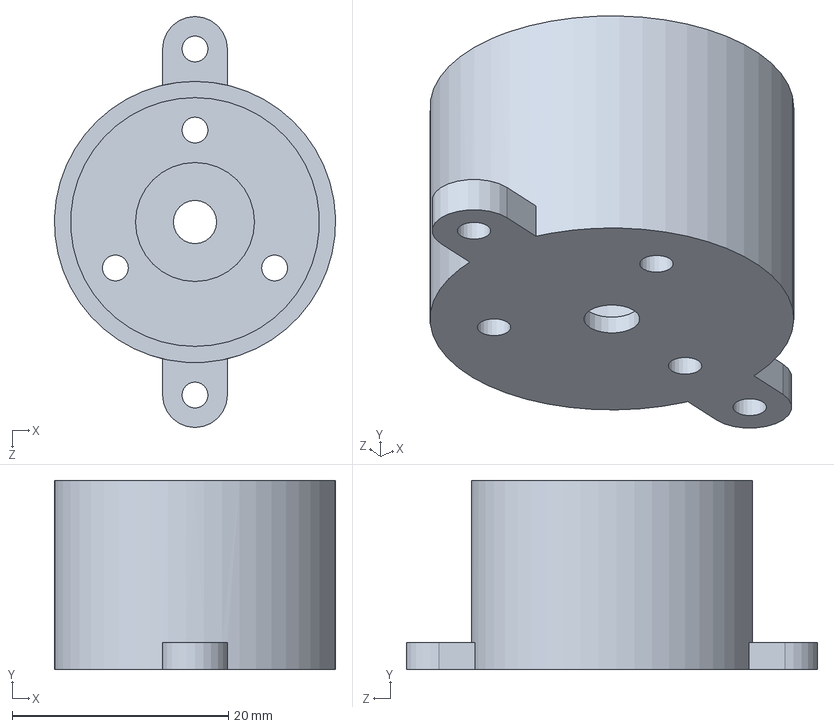
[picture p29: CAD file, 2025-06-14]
CAD_MECHANICAL_SYSTEM/DCXMount.SLDPRT
26.0 x 17.5 x 38.0 mm

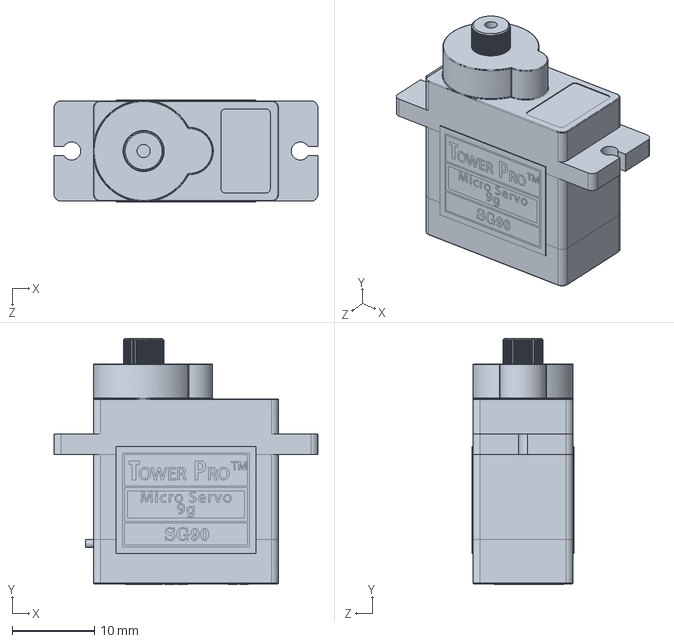
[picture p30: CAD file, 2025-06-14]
CAD_MECHANICAL_SYSTEM/SG90 - Micro Servo 9g - Tower Pro.1.SLDPRT
32.1 x 30.0 x 12.4 mm

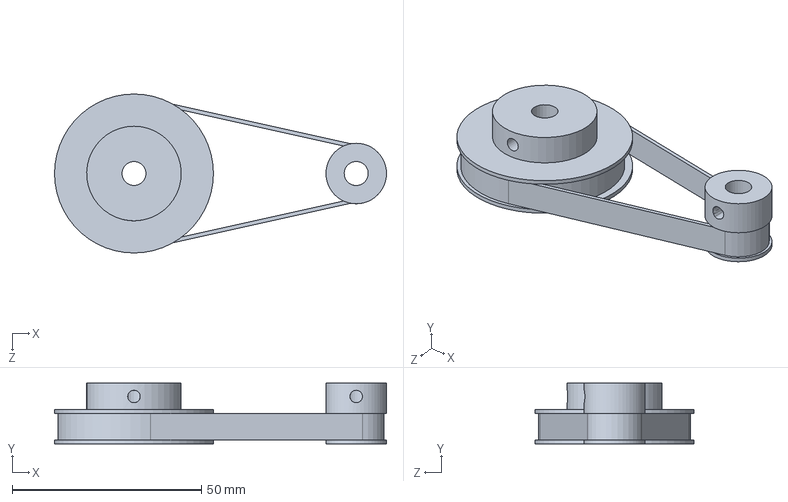
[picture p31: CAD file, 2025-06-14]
CAD_MECHANICAL_SYSTEM/Pulleys.SLDPRT
87.7 x 16.0 x 42.0 mm

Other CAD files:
CAD_MECHANICAL_SYSTEM/VShaft3.SLDPRT
CAD_MECHANICAL_SYSTEM/Magazine.SLDPRT
CAD_MECHANICAL_SYSTEM/SG90 - Micro Servo 9g - Tower Pro.2.SLDPRT
CAD_MECHANICAL_SYSTEM/ME507Base.SLDPRT
CAD_MECHANICAL_SYSTEM/BaseLid2.SLDPRT
CAD_MECHANICAL_SYSTEM/MaxonDCX.SLDPRT
CAD_MECHANICAL_SYSTEM/Shaftholder.SLDPRT
CAD_MECHANICAL_SYSTEM/Tensioner.SLDPRT
CAD_MECHANICAL_SYSTEM/VMotorMount.SLDPRT

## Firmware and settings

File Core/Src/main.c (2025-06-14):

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
/* Includes ------------------------------------------------------------------*/
#include "main.h"

/* USER CODE BEGIN Includes */
#include "motor.h"
#include "imu.h"
//#include "fsm.h"
#include <math.h>
#include <stdio.h>
#include <stdint.h>
#include <stdlib.h>
#include <string.h>
#include <ctype.h>
/* USER CODE END Includes */

/* USER CODE BEGIN PTD */
extern I2C_HandleTypeDef hi2c2;

volatile uint8_t imu_mode = 0;
volatile uint8_t calib_mode = 0;

volatile uint8_t lidar_mode = 0;
uint8_t lidar_buf[4];
/* USER CODE END PTD */

/* USER CODE BEGIN PD */
#define CPR_TURRET 3200
/* USER CODE END PD */

ADC_HandleTypeDef hadc1;

I2C_HandleTypeDef hi2c1;
I2C_HandleTypeDef hi2c2;

TIM_HandleTypeDef htim1;
TIM_HandleTypeDef htim2;
TIM_HandleTypeDef htim3;
TIM_HandleTypeDef htim9;
TIM_HandleTypeDef htim10;
TIM_HandleTypeDef htim11;

UART_HandleTypeDef huart1;

/* USER CODE BEGIN PV */
int32_t duty_flywheel1 = 0;
int32_t duty_flywheel2 = 0;
int32_t duty_turret1 = 0;
int32_t duty_turret2 = 0;

int32_t turret1_enc_count = 0;
int32_t turret1_enc_deg = 0;
int32_t turret1_target = 0;

int32_t turret2_enc_pos = 0;
int32_t turret2_enc_deg = 0;
int32_t turret2_target = 0;

motor_t flywheel1 = {
    .htim_forward = &htim1, .channel_forward = TIM_CHANNEL_1,
    .htim_reverse = &htim1, .channel_reverse = TIM_CHANNEL_4,
    .duty = 0, .target = 0, .actual = 0
};

motor_t flywheel2 = {
    .htim_forward = &htim9, .channel_forward = TIM_CHANNEL_1,
    .htim_reverse = &htim9, .channel_reverse = TIM_CHANNEL_2,
    .duty = 0, .target = 0, .actual = 0
};

motor_t turret1 = {
    .htim_forward = &htim1, .channel_forward = TIM_CHANNEL_2,
    .htim_reverse = &htim1, .channel_reverse = TIM_CHANNEL_3,
    .duty = 0, .target = 0, .actual = 0
};

motor_t turret2 = {
    .htim_forward = &htim10, .channel_forward = TIM_CHANNEL_1,
    .htim_reverse = &htim11, .channel_reverse = TIM_CHANNEL_1,
    .duty = 0, .target = 0, .actual = 0
};

// Define FSM states
typedef enum {
    STATE_0,
    STATE_1,
	STATE_2,
	STATE_3,
	STATE_4,
	STATE_5,
	STATE_6
} State_t;
State_t current_state = STATE_0;

uint8_t auto_mode = 0;
uint8_t auto_mot = 0;
uint8_t auto_lidar = 0;
uint16_t scan_index = 0;

uint32_t turret_move_start = 0;
uint16_t min_scan_dist = 0xFFFF;
uint16_t min_scan_index = 0;
uint16_t scan_res = 20;
int scan_dist[20];
int scan_amp[20];

#define RX_BUFFER_SIZE 7
uint8_t rx_buffer[RX_BUFFER_SIZE];
uint8_t rx_index = 0;
char msg_int[64];
char msg_main[64];
/* USER CODE END PV */

void SystemClock_Config(void);
static void MX_GPIO_Init(void);
static void MX_ADC1_Init(void);
static void MX_I2C1_Init(void);
static void MX_I2C2_Init(void);
static void MX_TIM1_Init(void);
static void MX_TIM2_Init(void);
static void MX_TIM3_Init(void);
static void MX_TIM9_Init(void);
static void MX_TIM10_Init(void);
static void MX_TIM11_Init(void);
static void MX_USART1_UART_Init(void);
/* USER CODE BEGIN 0 */
// === Servo Software PWM ===
void dwt_init(void) {
    CoreDebug->DEMCR |= CoreDebug_DEMCR_TRCENA_Msk;
    DWT->CYCCNT = 0;
    DWT->CTRL |= DWT_CTRL_CYCCNTENA_Msk;
}

uint16_t servo_angle = 140;  // global control variable
uint16_t servo_step = 0;
uint32_t servo_step_time = 0;

void servo_pwm_update(void) {
    static enum { IDLE, HIGH, LOW } state	 = IDLE;
    static uint32_t pulse_start_us = 0;
    static uint32_t period_start_us = 0;
    uint32_t now_us = DWT->CYCCNT / (SystemCoreClock / 1000000);

    uint32_t pulse_width_us = 1000 + ((uint32_t)servo_angle * 1000) / 180;

    switch (state) {
        case IDLE:
            HAL_GPIO_WritePin(GPIOA, GPIO_PIN_6, GPIO_PIN_SET);
            pulse_start_us = now_us;
            period_start_us = now_us;
            state = HIGH;
            break;
        case HIGH:
            if ((now_us - pulse_start_us) >= pulse_width_us) {
                HAL_GPIO_WritePin(GPIOA, GPIO_PIN_6, GPIO_PIN_RESET);
                state = LOW;
            }
            break;
        case LOW:
            if ((now_us - period_start_us) >= 20000) {
                state = IDLE;
            }
            break;
    }
}
/* USER CODE END 0 */

/**
  * @brief Main entry point — configures peripherals and enters control loop
  * @retval int
  */
int main(void)
{

  /* MCU Configuration--------------------------------------------------------*/

  /* Reset of all peripherals, Initializes the Flash interface and the Systick. */
  HAL_Init();

  /* Configure the system clock */
  SystemClock_Config();

  /* Initialize all configured peripherals */
  MX_GPIO_Init();
  MX_ADC1_Init();
  MX_I2C1_Init();
  MX_I2C2_Init();
  MX_TIM1_Init();
  MX_TIM2_Init();
  MX_TIM3_Init();
  MX_TIM9_Init();
  MX_TIM10_Init();
  MX_TIM11_Init();
  MX_USART1_UART_Init();
  /* USER CODE BEGIN 2 */
  HAL_TIM_PWM_Start(&htim1, TIM_CHANNEL_1);
  HAL_TIMEx_PWMN_Start(&htim1, TIM_CHANNEL_2);
  HAL_TIMEx_PWMN_Start(&htim1, TIM_CHANNEL_3);
  HAL_TIM_PWM_Start(&htim1, TIM_CHANNEL_4);
  HAL_TIM_PWM_Start(&htim9, TIM_CHANNEL_1);
  HAL_TIM_PWM_Start(&htim9, TIM_CHANNEL_2);
  HAL_TIM_PWM_Start(&htim10, TIM_CHANNEL_1);
  HAL_TIM_PWM_Start(&htim11, TIM_CHANNEL_1);
  HAL_TIM_Encoder_Start(&htim2, TIM_CHANNEL_ALL);
  HAL_TIM_Encoder_Start(&htim3, TIM_CHANNEL_ALL);
  HAL_GPIO_WritePin(GPIOB, GPIO_PIN_13, GPIO_PIN_RESET); // Force TF_Luna into I2C mode
  HAL_GPIO_WritePin(GPIOB, GPIO_PIN_12, GPIO_PIN_SET);  // Drive IMU RESET PIN high
  HAL_Delay(100);  // Optional but useful
  dwt_init();            // For accurate microsecond delay
  HAL_GPIO_WritePin(GPIOA, GPIO_PIN_6, GPIO_PIN_RESET);  // Initialize servo pin low
  HAL_Delay(100);

  // LUNA LIDAR I2C Check
  if (HAL_I2C_IsDeviceReady(&hi2c2, 0x10 << 1, 3, 100) == HAL_OK) {
      HAL_UART_Transmit(&huart1, (uint8_t*)"TF-Luna ready!\r\n", 17, HAL_MAX_DELAY);
  } else {
      HAL_UART_Transmit(&huart1, (uint8_t*)"TF-Luna NOT responding\r\n", 25, HAL_MAX_DELAY);
  }

  // BNO055 IMU I2C Check
  // #define BNO055_ADDR (0x29 << 1)  // 7-bit address shifted for STM32 HAL

  if (HAL_I2C_IsDeviceReady(&hi2c1, BNO055_ADDR, 3, 100) == HAL_OK) {
	  HAL_UART_Transmit(&huart1, (uint8_t*)"BNO055 ready!\r\n", 16, HAL_MAX_DELAY);
  } else {
   	  HAL_UART_Transmit(&huart1, (uint8_t*)"BNO055 NOT responding\r\n", 25, HAL_MAX_DELAY);
  }

  // IMU Init
  BNO055_Init(&hi2c1);
  //BNO055_StartCalibration();

  //uint8_t sys, gyr, acc, mag;
  //BNO055_GetCalibStatus(&sys, &gyr, &acc, &mag);
  //int len = sprintf(msg_main, "Calib SYS:%d GYR:%d ACC:%d MAG:%d\r\n", sys, gyr, acc, mag);
  //HAL_UART_Transmit(&huart1, (uint8_t*)msg_main, len, HAL_MAX_DELAY);
  HAL_Delay(100);
  int len = sprintf(msg_main, "Ping Pong Bot Starting...\r\n");
  HAL_UART_Transmit(&huart1, (uint8_t*)msg_main, len, HAL_MAX_DELAY);
  HAL_UART_Receive_IT(&huart1, &rx_buffer[rx_index], 1);
  /* USER CODE END 2 */

  /* Infinite loop */
  /* USER CODE BEGIN WHILE */
  int32_t turret1_enc_last = -1;
  int16_t turret2_enc_last = -1;
  uint8_t printed = 0;
  float heading, roll, pitch;
  int32_t imu_head_deg10 = 0;
  int32_t imu_roll_deg10 = 0;
  HAL_Delay(1000);
  //FSM_Init();
  while (1)
  {
    /* USER CODE END WHILE */

    /* USER CODE BEGIN 3 */
		//uint8_t mode = 0x00;
		//HAL_I2C_Mem_Write(&hi2c1, (0x29 << 1), 0x3D, I2C_MEMADD_SIZE_8BIT, &mode, 1, 10);
		//BNO055_ReadEuler(&heading,&roll,&pitch);
		//imu_head_deg10 = (int32_t)(heading*10.0f);
		//imu_roll_deg10 = (int32_t)(roll*10.0f);
		//HAL_Delay(20);
	    if (imu_mode) {
	        //float heading, roll, pitch;
	        //BNO055_ReadEuler(&heading, &roll, &pitch);

	        //int len = sprintf(msg_main, "H: %.1f R: %.1f P: %.1f\r\n", heading / 16.0f, roll / 16.0f, pitch / 16.0f);
	        int len = sprintf(msg_main, "H: %.1f R: %.1f P: %.1f\r\n", heading, roll, pitch);
	    	HAL_UART_Transmit(&huart1, (uint8_t*)msg_main, len, HAL_MAX_DELAY);
	        len = sprintf(msg_main, "H: %d R: %d\r\n",imu_head_deg10,imu_roll_deg10);
	    	HAL_UART_Transmit(&huart1, (uint8_t*)msg_main, len, HAL_MAX_DELAY);

	        HAL_Delay(500);  // Limit update rate
	    }

	  // ENCODERS
	  turret1_enc_count = __HAL_TIM_GET_COUNTER(&htim2);
	  if (turret1_enc_count != turret1_enc_last) {
	      turret1_enc_deg = (7200 * turret1_enc_count) / (3200*10); // 7200 = 360.0 deg × 20 (tenths)
 	      turret1_enc_last = turret1_enc_count;
	  }
	  int16_t turret2_enc_now = (int16_t)__HAL_TIM_GET_COUNTER(&htim3);
	  int16_t delta = turret2_enc_now - turret2_enc_last;
      turret2_enc_last = turret2_enc_now;
      turret2_enc_pos += delta;
      turret2_enc_deg = (7200 * turret2_enc_pos) / (3200*10); // degrees × 10
      //turret1_enc_deg = imu_roll_deg10;
      // SOFTWARE PWM
      servo_pwm_update();
      // FINITE-STATE-MACHINE
      switch(current_state)
      {
      	  //int len;
      	  case STATE_0: // Initialize
      		  turret1_target = -150;
      		  turret2_target = 30;
				if (turret_move_start == 0) {
					turret_move_start = HAL_GetTick();
				}
      		  //turret1_target = 0;
      		  //turret2_target = 0;
      		  move_to(&turret1, turret1_target, turret1_enc_deg);
      		  move_to(&turret2, turret2_target, turret2_enc_deg);
      		  //if (HAL_GetTick() - turret_move_start >= 2000)
      		  if (abs(turret1_target - turret1_enc_deg) < 5 && abs(turret2_target - turret2_enc_deg) < 5)
      		  {
      		      turret_move_start = 0;
      		      //enable(&turret2);
      			  current_state = STATE_1;
      		      int len = sprintf(msg_main, "Motors Initialized\r\n");
    	          HAL_UART_Transmit(&huart1, (uint8_t*)msg_main, len, HAL_MAX_DELAY);
      		  }
      		  break;
      	  case STATE_1: // Hub
      		  if (!printed) {
      			  int len = sprintf(msg_main, "Waiting Command...\r\n");
    	          HAL_UART_Transmit(&huart1, (uint8_t*)msg_main, len, HAL_MAX_DELAY);
      			  printed = 1;
      		  }
      		  break;
			case STATE_2: // Move turret
			{
				// Start timing on first entry into this state
				if (turret_move_start == 0) {
					turret_move_start = HAL_GetTick();
				}
					move_to(&turret1, turret1_target, turret1_enc_deg);
					move_to(&turret2, turret2_target, turret2_enc_deg);

					// Wait 1 second before considering the move "complete"
					if (abs(turret1_target - turret1_enc_deg) < 5 && abs(turret2_target - turret2_enc_deg) < 5){
					//if (HAL_GetTick() - turret_move_start >= 1000) {
						turret_move_start = 0;  // Reset for next use
						enable(&turret1);
						enable(&turret2);
						//int len = sprintf(msg_main, "Turret Move Timed Out\r\n");
						//HAL_UART_Transmit(&huart1, (uint8_t*)msg_main, len, HAL_MAX_DELAY);
						if (auto_mode == 0){
							current_state = STATE_1;
							printed = 0;
						}
						else {
							auto_mot = 1;
							current_state = STATE_6;
						}
					}
			}
			break;
      	  case STATE_3: // Lidar
      	  {
      		  uint8_t reg = 0x00;
      	      uint16_t dist = 0;
      	      uint16_t amp = 0;
      	      if (HAL_I2C_Master_Transmit(&hi2c2, 0x10 << 1, &reg, 1, 10) == HAL_OK &&
      	      	  HAL_I2C_Master_Receive(&hi2c2, 0x10 << 1, lidar_buf, 4, 10) == HAL_OK) {
      	      	  dist = lidar_buf[0] | (lidar_buf[1] << 8);
      	      	  amp  = lidar_buf[2] | (lidar_buf[3] << 8);
      	      } else {

      	      }
	          if (auto_mode == 0){
	      	      int len = sprintf(msg_main, "Dist: %d cm, Amp: %d\r\n", dist, amp);
		          HAL_UART_Transmit(&huart1, (uint8_t*)msg_main, len, HAL_MAX_DELAY);
		          current_state = STATE_1;
		          printed = 0;
	          }
	          else {
	      	      int len = sprintf(msg_main, "Auto Dist: %d cm, Amp: %d\r\n", dist, amp);
		          HAL_UART_Transmit(&huart1, (uint8_t*)msg_main, len, HAL_MAX_DELAY);
		          scan_dist[scan_index] = dist;
		          scan_amp[scan_index] = amp;
		          if (dist < min_scan_dist && amp > 100) {
		              min_scan_dist = dist;
		              min_scan_index = scan_index;
		          }
		          current_state = STATE_6;
		          auto_lidar = 1;
	          }
      	  }
	      break;
      	  case STATE_4: // Flywheels
      	  {
      		  set_duty(&flywheel1, duty_flywheel1);
	          int len = sprintf(msg_main, "Flywheel Speed Set\r\n");
	          HAL_UART_Transmit(&huart1, (uint8_t*)msg_main, len, HAL_MAX_DELAY);
      		  if (auto_mode == 0){
      			  current_state = STATE_1;
      			  printed = 0;
      		  }
      		  else {
      			  current_state = STATE_6;
      		  }
      	  }
          break;
      	  case STATE_5: // launch
      	  {
      	    //int len = sprintf(msg_main, "Servo state: %d\r\n", servo_step);
      	    //HAL_UART_Transmit(&huart1, (uint8_t*)msg_main, len, HAL_MAX_DELAY);
      	    switch (servo_step) {
      	        case 0:
      	            servo_angle = 320;  // move back
      	            servo_step_time = HAL_GetTick();
      	            servo_step = 1;
      	            break;
      	        case 1:
      	            if (HAL_GetTick() - servo_step_time >= 300) {
      	                servo_angle = 140;  // move forward
      	                servo_step_time = HAL_GetTick();
      	                servo_step = 2;
      	            }
      	            break;
      	        case 2:
      	            if (HAL_GetTick() - servo_step_time >= 300) {
      	                servo_angle = 140;  // return to center
      	                if (auto_mode == 0){
      	                	current_state = STATE_1;
      	                	printed = 0;
      	                	servo_step = 0;
      	                }
      	                else {
      	                	current_state = STATE_6;
      	                	servo_step = 0;  // reset step
      	                }
      	            }
      	            break;
      	    }
      	}
      	break;
      	case STATE_6: // Auto scan
      	{
      		HAL_Delay(50); // Avoid console clogging
      		if (scan_index < 20){
      			if (auto_mot == 0){
      				turret2_target = (10*scan_index);
      				current_state = STATE_2;
            	    //int len = sprintf(msg_main, "Motor Movement %d \r\n", scan_index);
      	            //HAL_UART_Transmit(&huart1, (uint8_t*)msg_main, len, HAL_MAX_DELAY);
      			}
      			else if (auto_lidar == 0){
      				current_state = STATE_3;
            	    //int len = sprintf(msg_main, "LIDAR Scan %d \r\n", scan_index);
      	            //HAL_UART_Transmit(&huart1, (uint8_t*)msg_main, len, HAL_MAX_DELAY);
      			}
      			else if (auto_mot == 1 && auto_lidar == 1){
      				scan_index += 1;
      				auto_mot = 0;
      				auto_lidar = 0;
      			}
      		}
      		else if (scan_index == 20){
      		    // Reset scan for next time
      		    if (min_scan_dist > 450){
      		    	int len = sprintf(msg_main,"No object in range");
      		    	HAL_UART_Transmit(&huart1, (uint8_t*)msg_main, len, HAL_MAX_DELAY);
      		    	scan_index = 24;
      		    }
      		    else {//scan_index = 0;
          		    len = sprintf(msg_main, "Scan complete. Closest at index %d, dist %d cm\r\n",
          		                      min_scan_index, min_scan_dist);
          		    HAL_UART_Transmit(&huart1, (uint8_t*)msg_main, len, HAL_MAX_DELAY);
      		    	//min_scan_index = 0;
      		    	turret2_target = (10*min_scan_index);
      		    	//turret1_target = -180;
      		    	scan_index = 21;
      		    	current_state = STATE_2;
      		    }
      		}
      		else if (scan_index == 21){
      			if (min_scan_dist < 100){
      				duty_flywheel1 = 85;
      			}
      			else if (min_scan_dist < 250){
      				duty_flywheel1 = 90;
      			}
      			else {
      				duty_flywheel1 = 100;
      			}
      			current_state = STATE_4;
      			scan_index = 22;
      		}
      		else if (scan_index == 22){
      			current_state = STATE_5;
      			scan_index = 23;
      		}
      		else if (scan_index == 23){
      			duty_flywheel1 = 0;
      			current_state = 4;
      			scan_index = 24;
      		}
      		else if (scan_index == 24){
      			auto_mode = 0;
      			printed = 0;
      			scan_index = 0;
      			min_scan_dist = 0xFFFF;
      			min_scan_index = 0;
      			current_state = STATE_1;
      		}
      		else {
        	    int len = sprintf(msg_main, "BROKEN CODE");
        	   	HAL_UART_Transmit(&huart1, (uint8_t*)msg_main, len, HAL_MAX_DELAY);
        	   	scan_index = 0;
        	   	current_state = STATE_1;
      		}
        }
      	break;
      }
	}
  /* USER CODE END 3 */
}
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

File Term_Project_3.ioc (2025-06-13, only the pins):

Mcu.UserName=STM32F411CEUx
PA0-WKUP.Signal=SharedAnalog_PA0
PA1.Signal=S_TIM2_CH2
PA10.Signal=USART1_RX
PA11.Signal=S_TIM1_CH4
PA13.Signal=SYS_JTMS-SWDIO
PA14.Signal=SYS_JTCK-SWCLK
PA15.Signal=S_TIM2_CH1_ETR
PA2.Signal=S_TIM9_CH1
PA3.Signal=S_TIM9_CH2
PA6.Signal=GPIO_Output
PA7.Signal=GPIO_Output
PA8.Signal=S_TIM1_CH1
PA9.Signal=USART1_TX
PB0.Signal=TIM1_CH2N
PB1.Signal=TIM1_CH3N
PB10.Signal=I2C2_SCL
PB12.Signal=GPIO_Output
PB13.Signal=GPIO_Output
PB3.Signal=I2C2_SDA
PB4.Signal=S_TIM3_CH1
PB5.Signal=S_TIM3_CH2
PB6.Signal=I2C1_SCL
PB7.Signal=I2C1_SDA
PB8.Signal=S_TIM10_CH1
PB9.Signal=S_TIM11_CH1

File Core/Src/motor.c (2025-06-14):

/**
 * @file motor.c
 * @brief Implementation of bidirectional PWM motor driver functions
 *
 * Provides PWM control for motors using two timer channels (forward and reverse).
 * Includes proportional control logic to move toward target angles for turret motors.
 */

#include "motor.h"
#include "main.h"
#include <stdio.h>
#include <stdlib.h>

#define PWM_MAX 2399


/**
 * @brief Set the motor's PWM output based on signed duty cycle
 *
 * Adjusts direction and magnitude using complementary PWM logic.
 * For turret1, logic is inverted to account for wiring or mechanical setup.
 */
void set_duty(motor_t* motor, int32_t duty)
{
    // Invert logic for turret1 using complementary outputs
    extern motor_t turret1;
    if (motor == &turret1)
    {
        if (duty > 0) duty = 100 - duty;
        else if (duty < 0) duty = -(100 + duty); // e.g. -30 → -70
    }

    if (duty > 100) duty = 100;
    if (duty < -100) duty = -100;

    uint32_t pwm_val_fwd = motor->htim_forward->Init.Period * abs(duty) / 100;
    uint32_t pwm_val_rev = motor->htim_reverse->Init.Period * abs(duty) / 100;
    motor->duty = duty;

    if (duty > 0)
    {
        // Forward: PWM on IN1, LOW on IN2
        HAL_TIM_PWM_Start(motor->htim_forward, motor->channel_forward);
        HAL_TIM_PWM_Stop(motor->htim_reverse, motor->channel_reverse);

        __HAL_TIM_SET_COMPARE(motor->htim_forward, motor->channel_forward, pwm_val_fwd);
        __HAL_TIM_SET_COMPARE(motor->htim_reverse, motor->channel_reverse, 0);
    }
    else if (duty < 0)
    {
        // Reverse: PWM on IN2, LOW on IN1
        HAL_TIM_PWM_Stop(motor->htim_forward, motor->channel_forward);
        HAL_TIM_PWM_Start(motor->htim_reverse, motor->channel_reverse);

        __HAL_TIM_SET_COMPARE(motor->htim_forward, motor->channel_forward, 0);
        __HAL_TIM_SET_COMPARE(motor->htim_reverse, motor->channel_reverse, pwm_val_rev);
    }
    else
    {
        // Coast: both low
        HAL_TIM_PWM_Stop(motor->htim_forward, motor->channel_forward);
        HAL_TIM_PWM_Stop(motor->htim_reverse, motor->channel_reverse);

        __HAL_TIM_SET_COMPARE(motor->htim_forward, motor->channel_forward, 0);
        __HAL_TIM_SET_COMPARE(motor->htim_reverse, motor->channel_reverse, 0);
    }
}

/**
 * @brief Move the motor toward a target using proportional control
 *
 * Uses a simple P-controller with anti-windup and deadband handling.
 */
void move_to(motor_t* p_mot, int32_t target, int32_t actual)
{
    int32_t error = target - actual;
    int32_t duty = 0;

    // Deadband threshold
    /*if (abs(error) < 2) {
        set_duty(p_mot, 0); // Stop the motor
        return;
    }*/

    // Proportional gain (tune as needed)
    float Kp = 0.9f;

    // Proportional control calculation
    duty = (int32_t)(Kp * error);

    // Apply minimum duty to overcome static friction
    if (duty > 0 && duty < 50)
        duty = 50;
    else if (duty < 0 && duty > -50)
        duty = -50;

    // Clamp to safe duty limits
    if (duty > 80) duty = 80;
    if (duty < -80) duty = -80;

    set_duty(p_mot, duty);
}

/**
 * @brief Disable PWM output (stop both channels)
 */
void disable(motor_t* p_mot)
{
    HAL_TIM_PWM_Stop(p_mot->htim_forward, p_mot->channel_forward);
    HAL_TIM_PWM_Stop(p_mot->htim_reverse, p_mot->channel_reverse);
}

/**
 * @brief Enable both channels to full PWM output
 */
void enable(motor_t* p_mot)
{
    HAL_TIM_PWM_Start(p_mot->htim_forward, p_mot->channel_forward);
    HAL_TIM_PWM_Start(p_mot->htim_reverse, p_mot->channel_reverse);
    __HAL_TIM_SET_COMPARE(p_mot->htim_forward, p_mot->channel_forward, PWM_MAX);
    __HAL_TIM_SET_COMPARE(p_mot->htim_reverse, p_mot->channel_reverse, PWM_MAX);
}

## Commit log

2025-06-05 Current COde
    Nolan's Zip File
2025-06-05 Added Encoder and Updated IOC
2025-06-05 IDK
    Making the code openable on my STM32Cube_IDE
2025-06-14 SolidWorks assembly and parts files
    [37d-gearmotor-50-70-encoder.SLDPRT, 7-Bearing.SLDPRT, BaseLid2.SLDPRT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]
2025-06-14 CAD -> gitignore
    [37d-gearmotor-50-70-encoder.SLDPRT, 7-Bearing.SLDPRT, BaseLid2.SLDPRT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]
2025-06-14 Folder for Mechanical System Design
    [37d-gearmotor-50-70-encoder.SLDPRT, 7-Bearing.SLDPRT, BaseLid2.SLDPRT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]
